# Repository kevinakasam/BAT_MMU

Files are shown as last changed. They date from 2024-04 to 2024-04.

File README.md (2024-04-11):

# The BAT MMU - a simple 2 channel MMU

Side view        |  Top view   |  Hr_Ravn view   
:-------------------------:|:-------------------------:|:-------------------------:
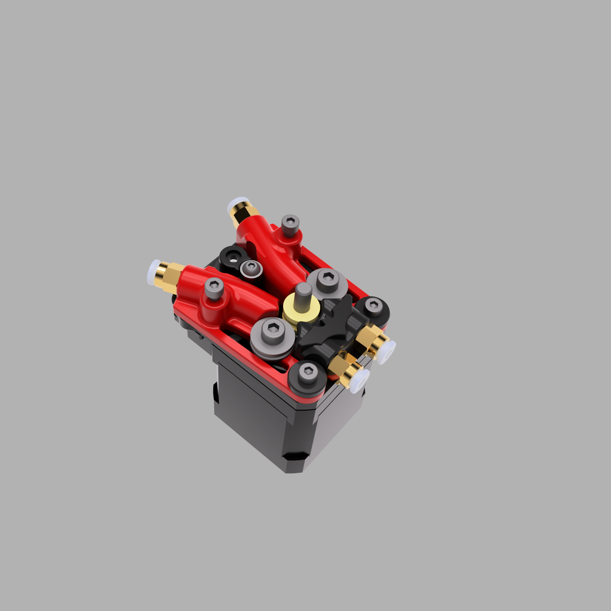
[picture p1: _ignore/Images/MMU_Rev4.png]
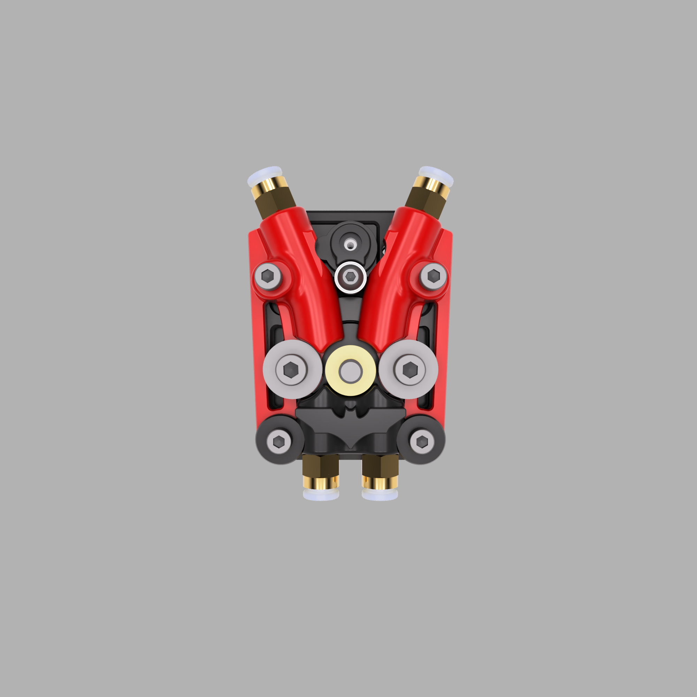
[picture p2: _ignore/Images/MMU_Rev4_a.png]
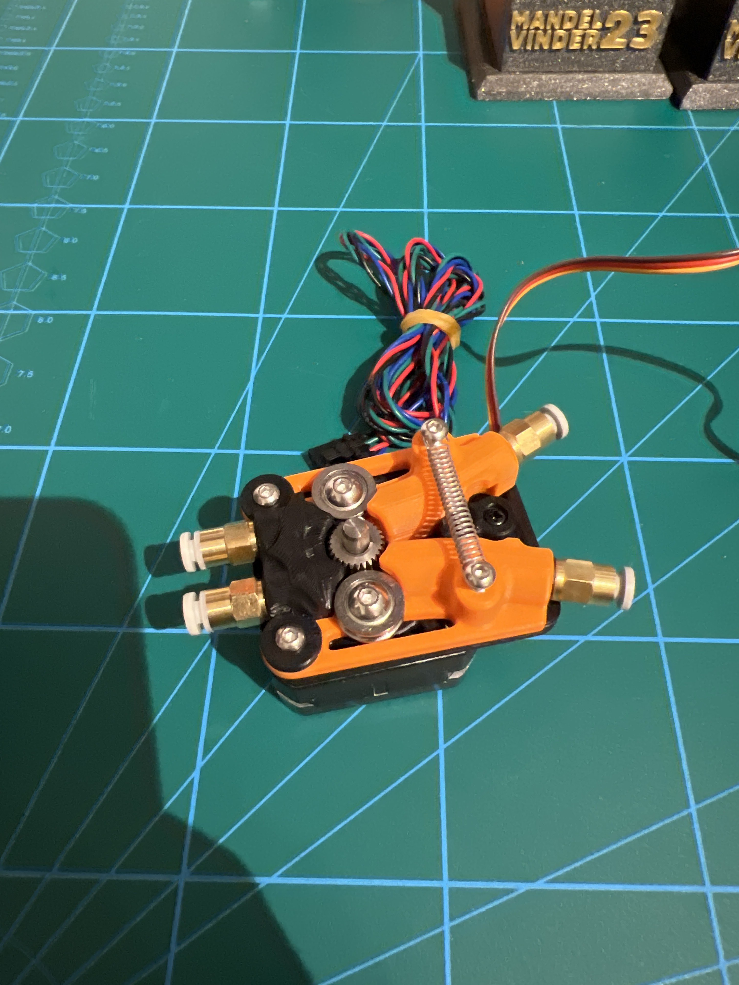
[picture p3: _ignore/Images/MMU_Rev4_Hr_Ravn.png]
  |   |  

Sooo... this is a very old but cool project, I think. I started this project over two years ago, somewhere in 2022, I think. At least, that's when I made the first post about it on Discord. However, let me tell you a bit about the how, why, when, and what's left to do:

### What is this?

It's a two-channel MMU made out of the bare basics you need to swap filaments. That being said, the term MMU, also *Multi* Material Unit, might be a bit over the top as it only swaps two colors (a little spoiler on a crazy idea is at the very end of this page). But two colors are already enough for 95% of the multi-color prints I do, like logos on parts, mesh skirts, and such things. In other words, it's for the lazy people who don't want to swap the colors manually by hand. As another bonus, Bat could also manage two spools on your printer. If you're like me, you print mostly with the same colors, e.g., black and white. So rather than swapping out the filament manually for a (single color) print, you can simply select the filament in the slicer and let the printer check if the correct filament is loaded (that's what I use it for mostly). Or what about a runout manager? In an endless spool mode, Bat *can* / could change the spool once one got empty. There are many use cases for a two-channel MMU, especially for us lazy people.

### How does it work?

Bat is a super simple system which is basically made out of one motor being the extruder and one servo being the selector. Looking at a normal bowden extruder, the motor feeds and retracts one filament by moving back and forward, but for that only *one side* of the extruder is used. Imagine you split a bowden extruder in half and mirror the sides, then you have a filament on each side of it. And this is the basic layout of the Bat MMU. In order to control which filament gets fed / retracted, the servo can move the idler arms on each side of the extruder. By pushing the arm away from the extruder gear, the filament won't move (the filament is deactivated). Due to the spring connection between both arms, the deactivation of one arm (pushing it away) will result in an activation of the other arm. That's it. The only thing we have to account for is that the motor has to spin the other way around for each filament. E.g., a clockwise motor movement feeds Filament A but will retract Filament B. The other way around, we have to invert the motor to feed Filament B / retract Filament A. This might sound a bit confusing, but you can take a look at the little demo video I added to this readme.

#### Demo / Assembly Video

Click on the image to get to the YouTube video:

<a href="https://youtu.be/mqmhv5pWaTc
" target="_blank">MMU Assembly</a> 

### BOM - What do I need to build one?

Coming from the Ender 3 ecosystem, the Bat MMU reuses basically the stock bowden extruder. Varying hardware shouldn't be too much work; I simply used what I have on hand. Modifying the parts e.g. for BMG gears shouldn't be that hard (due to their gears they would also act as dual drive). After building so many [Papilio's](https://kevinakasam.com/papilio/), I have an army of LGX / HGX extruder gears laying around, I thought about to use for a BAT MMU. But that's future talk.

**Here's what you need to build a Bat MMU and its supported alternatives:** [Google Spreadsheet](https://docs.google.com/spreadsheets/d/1bSXrbz5Jo8a5GIIJkao1ZaGwCmv6FLKUNqkR6fM1aHM/edit?usp=sharing) 

##### Alternatives / Experimentals

__Spring__

You can use a printed spring for testing, but I recommend a metal spring to get more tension on the filament. If your reversed bowden setup is very smooth, the printed one will do the job as well, but I don't have a long-time experience with it.

__Bearing__

You can use a printed bearing on the servo arm instead of a proper bearing. Thanks to Thomas for the idea! All the bearing has to do is to reduce the friction between the servo arm and the filament arms. By having a (printed) bearing on the arm, there aren't any rubbing faces, so the servo has an easier job.

### Why is it called Bat MMU?

In the first versions, the Servo was on top of the MMU unit to switch the arms. The shape of the servo reminded me of a bat, and then I made it look like an actual bat, and yeah, that gave it its name. Now, with the newest revision, the servo has moved, and the arm doesn't look like a bat anymore, but I still modeled one on there, so it's still a Bat MMU 😛 and you can also see the two filament arms as wings, so Bat again.

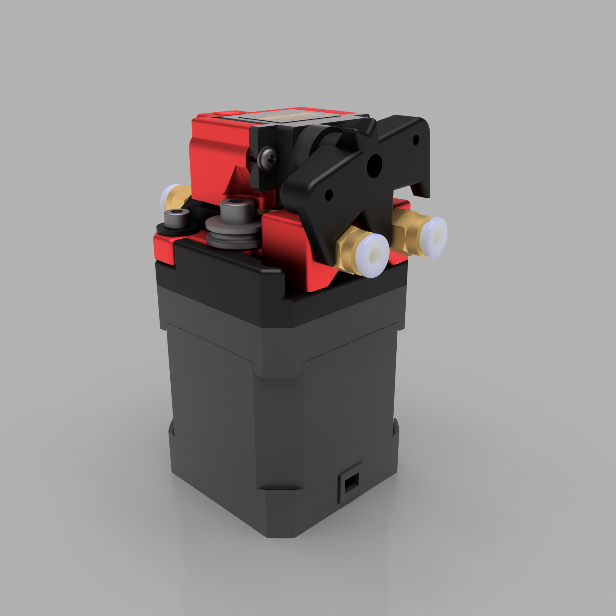
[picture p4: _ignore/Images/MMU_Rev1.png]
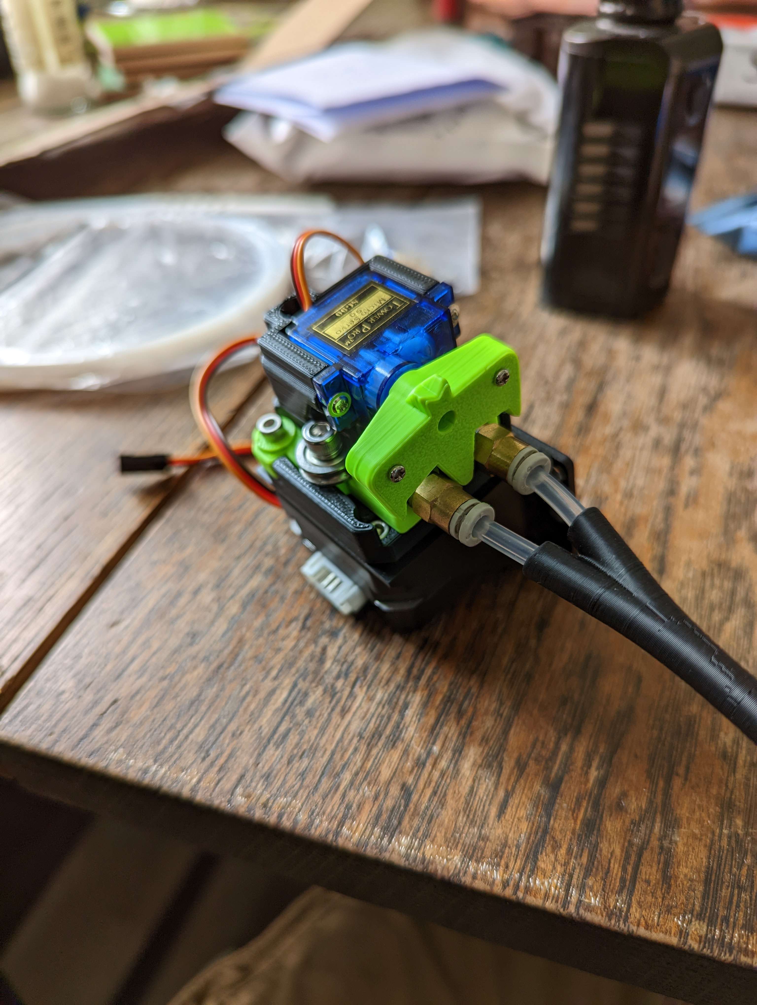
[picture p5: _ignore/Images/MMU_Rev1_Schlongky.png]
   

### The elephant in the room: What's left to do? / What the hell is this hacky code?

Yep, that's right. I might have the skills to sketch something up in CAD, but hell no, I'm not a programmer. I don't want to tell you that I spent easily over 100 hours making these Macros because they're kinda hacky. They do work, that's a plus, but it really relies on saving variables which isn't ideal for the system load, it double-checks some things, sometimes it's smarter than you and does unexpected things, and I think I really overcomplicated it. So far, you can use it for swapping filaments or multi-color prints, and it always remembers which filament is loaded, but functions like the mentioned endless spool mode aren't implemented yet.

##### Bugs

Known bugs are that the pausing during an error doesn't really pause the printer as it tries to complete the load/unload sequence, and for some reason, the movement logic for Filament B gets inverted on its own, no matter what the direction variable is set to (so it still does the right thing, but I don't know where it takes the knowledge from to move that way). Also, the idea to add unique Error codes didn't work out as planned because at some point I only used copy and paste and completely lost track of the numbering.

##### My hacky Macros 

As I have zero knowledge about writing any Python code for this, I had to use Klipper Macros to get this done. This means linking the MMU to the extruder for the final loading wasn't that easy, and I had to trick Klipper for that. By using the `[duplicate_pin_override]`, I could trick Klipper to believe that there are two motors on the MMU, one for feeding the filament to the extruder and one that *extrudes* the filament together with the actual extruder to load it into the nozzle (synced movement between MMU and extruder for loading). That way, the `manual_stepper BATMMU_stepper` and the `extruder_stepper BATMMU_extruder_stepper` are completely identical in the setup for pins, etc., but can be used differently with Klipper. The `manual_stepper BATMMU_stepper` takes care of all the filament movements to the extruder entry; from that point on, the `extruder_stepper BATMMU_extruder_stepper` does all movements together with the actual extruder till the toolhead sensor is triggered.

In short: The Code works, but the Code is evil.

##### My Dream of Happy Hare

It would be a dream to get [Happy Hare](https://github.com/moggieuk/Happy-Hare) support on this, but I don't know how as there's no homing sequence with an endstop involved (my code relies on the saved loaded filament variables), and we don't even have a selector. I think that could be a fun challenge, and if it works, we have a wonderful Bat MMU because the design itself works perfectly fine and so does Happy Hare.

### Are two channels all we can get?

Mh, no. I have two ideas I want to share with you. First, imagine a stack of two Bat MMUs on one stepper, so with two arms per side on top of each other. All they need are two more positions on the servo arm so still only one of the arms is activated / 3 are deactivated. I already started that at some point but never made it to a real design.

Second idea: Add a planetary drive. This will only make sense to you if you're familiar with planetary drives. Planetary drives have the advantage of having three moving components. Setting one as an input, there are always two left that can act as an output. This is partially correct as one of the two has to be stationary to make the planetary work. But setting the Sun as the input (the motor), there are the planets as output if the ring is stationary, or the ring as output if the planets are stationary. You can play around with that in this very cool simulator (https://www.thecatalystis.com/gears/) or watch this simulation: https://www.tec-science.com/wp-content/uploads/2018/09/en-planetary-gear-operation-modi.mp4

So maybe you got my idea already, but with a servo, we should be able to switch the planetary drive between these two output modes. This also means that one output can act as a selector and the other as a feeder. I started with a circular design with the planetary drive in the middle and all the filament paths around it. With that, you can theoretically use an infinite amount of filaments with the MMU; all you have to do is to increase the diameter of the planetary drive. An alternative idea was to use a more linear setup like from the ercf where the planetary gear drives along. All this is still very much in the "I had an idea" state, but I think this is super exciting as you could get infinite channels out of 10€ hardware.

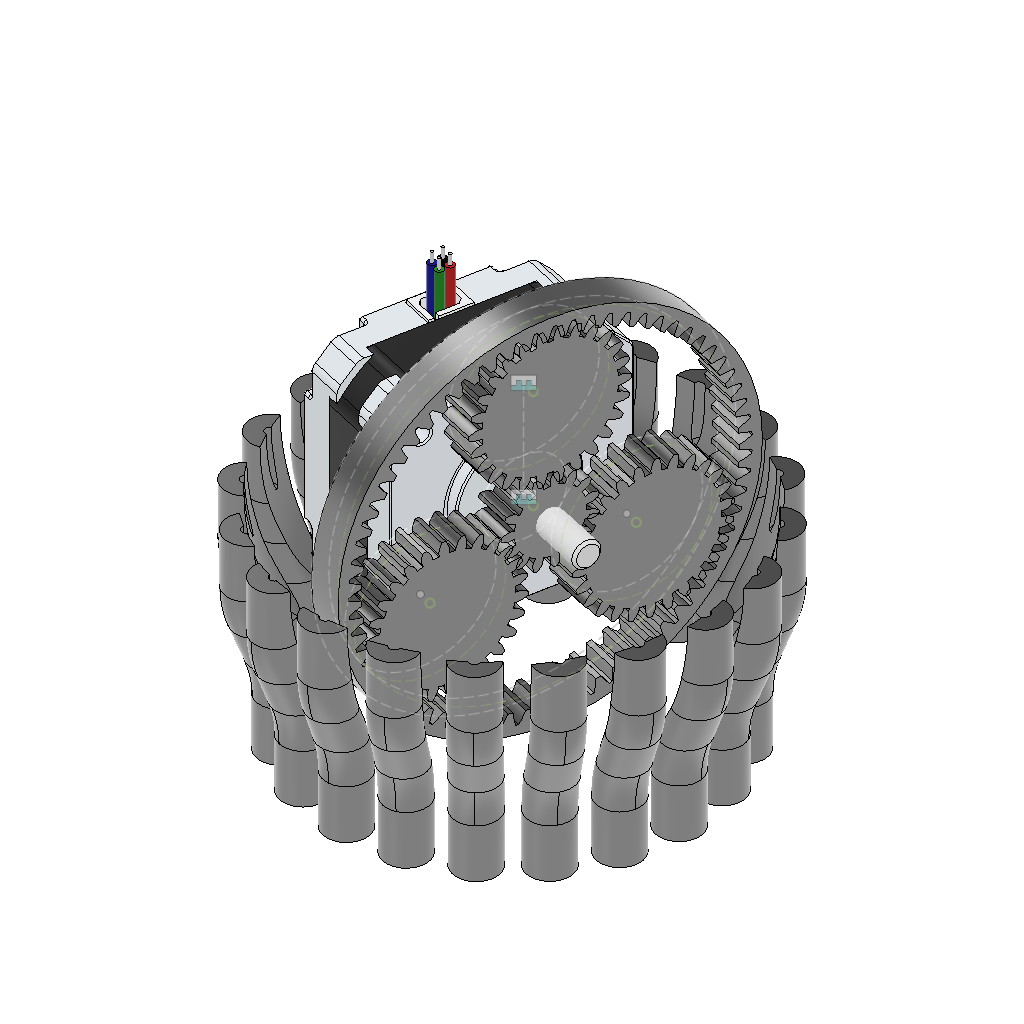
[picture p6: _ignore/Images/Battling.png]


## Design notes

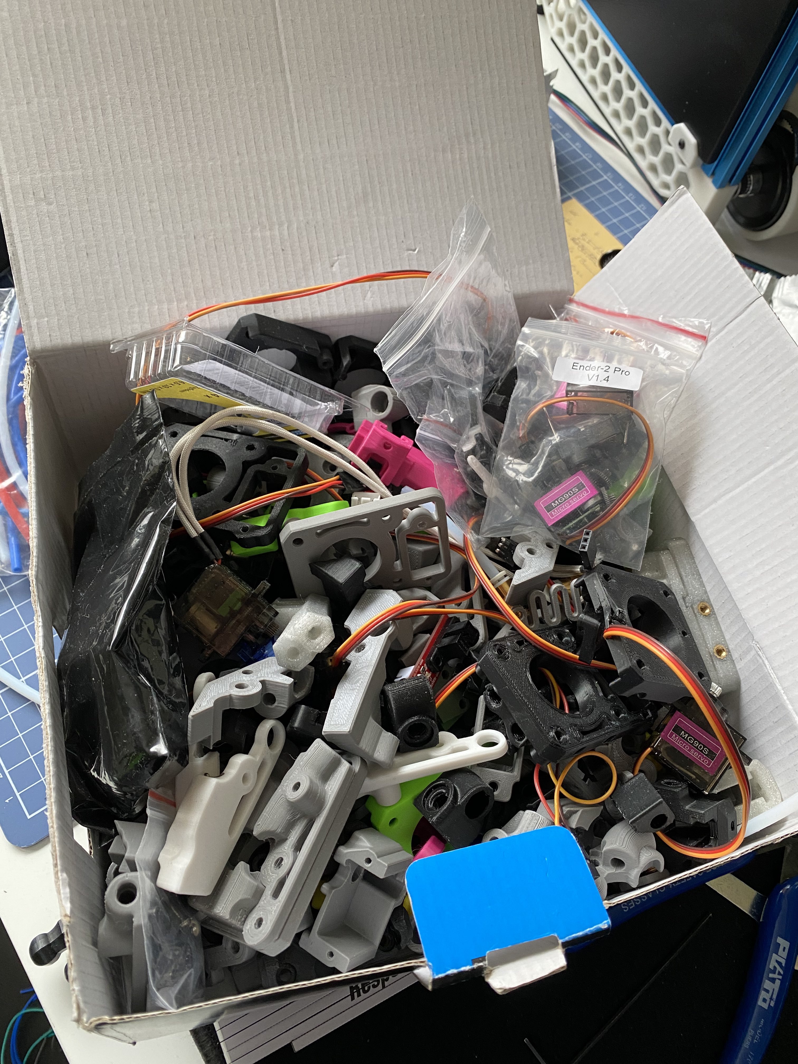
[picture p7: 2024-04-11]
_ignore/Images/its_fun_they_said.png

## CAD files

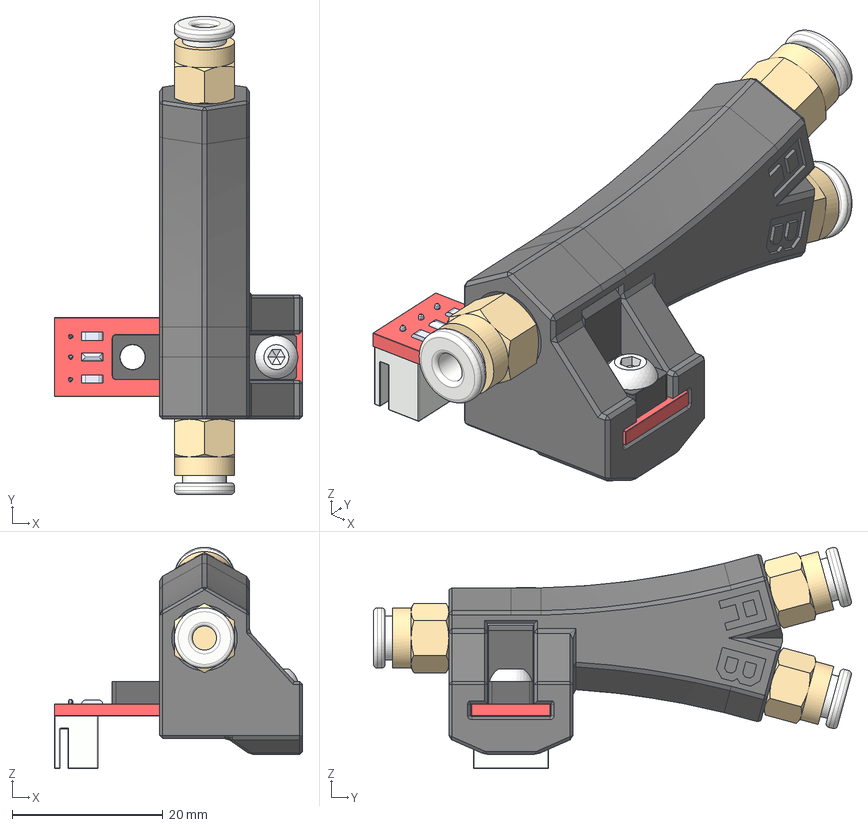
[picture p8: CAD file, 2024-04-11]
CAD/Optical_Y_Splitter_M6.step
33.0 x 63.5 x 29.4 mm
Optical Switch v1
SmartYSplitter
M6 Pneumatic joint x 2
M6 Pneumatic joint v2(Mirror)
M3X8 BHSC v1

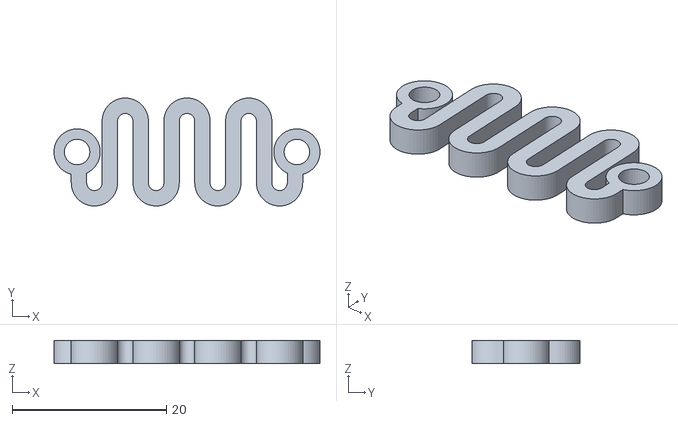
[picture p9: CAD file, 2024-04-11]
STL/MMU/Spring_printed_experimental.stl
34.5 x 14.0 x 3.00

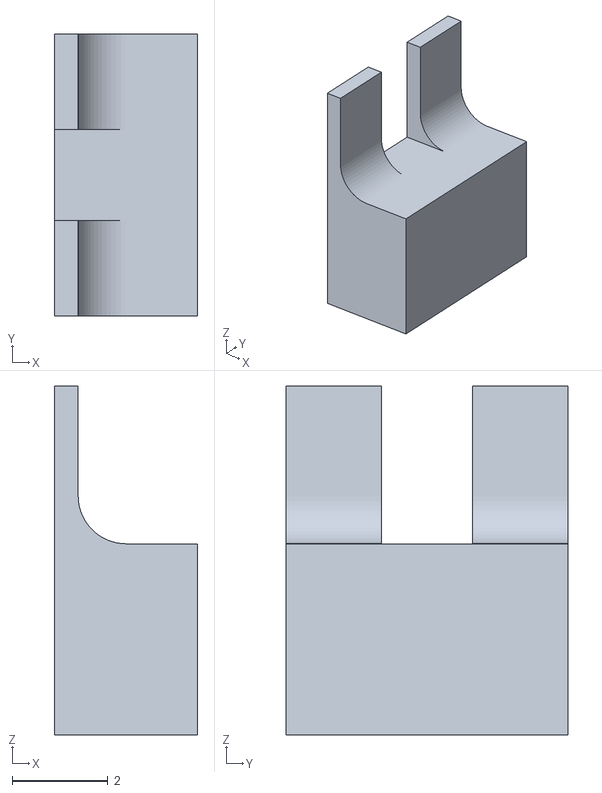
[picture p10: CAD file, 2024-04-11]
STL/Y Splitter/Optical_Y_Guide_Piece_For_Sensor.stl
3.00 x 5.90 x 7.30

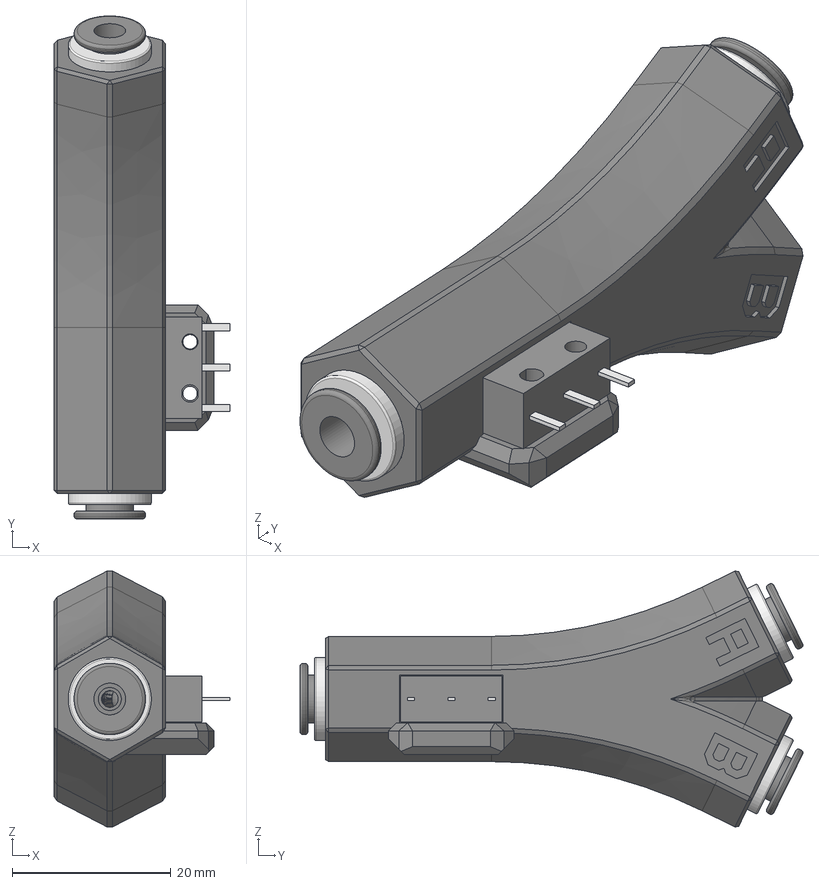
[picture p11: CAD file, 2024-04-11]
CAD/Omron_Y_Splitter_M10_and_ECAS.step
22.1 x 63.3 x 32.2 mm
SmartYSplitter
Omron_D2F_F v1
ECAS04 Bowden Collet v2 x 3

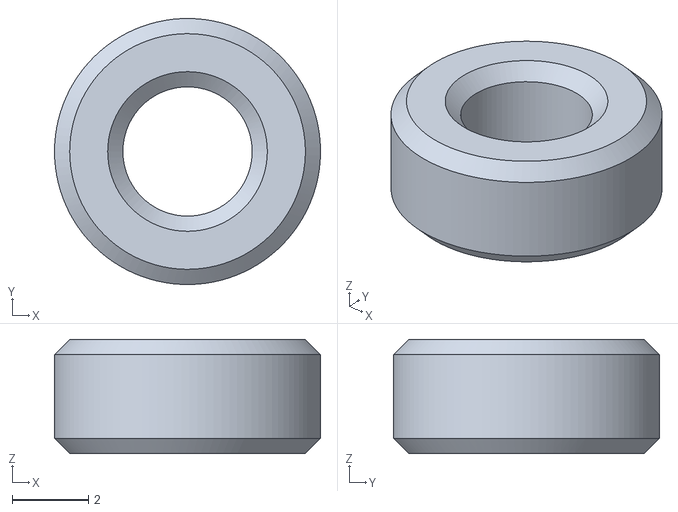
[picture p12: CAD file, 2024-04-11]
STL/MMU/ServoArm_Bearing_Printed_Experimental.stl
7.00 x 7.00 x 3.00

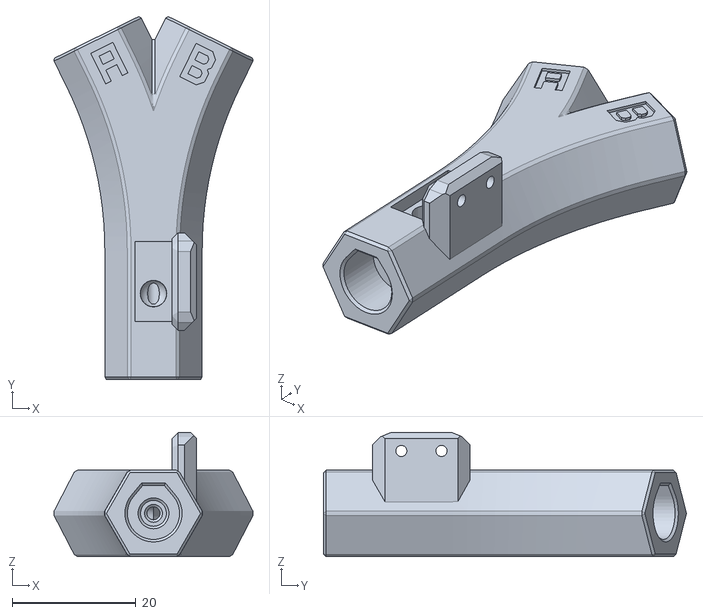
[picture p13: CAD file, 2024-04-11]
STL/Y Splitter/Omron_Y_ECAS.stl
32.2 x 58.8 x 20.1

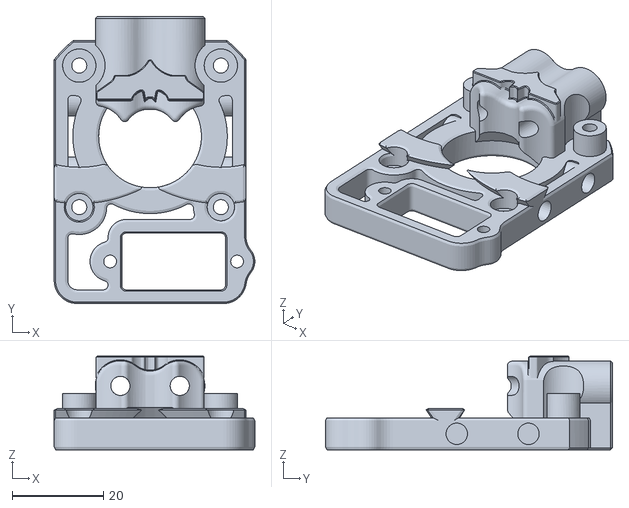
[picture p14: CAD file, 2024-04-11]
STL/MMU/Base_ECAS.stl
43.9 x 62.8 x 20.5

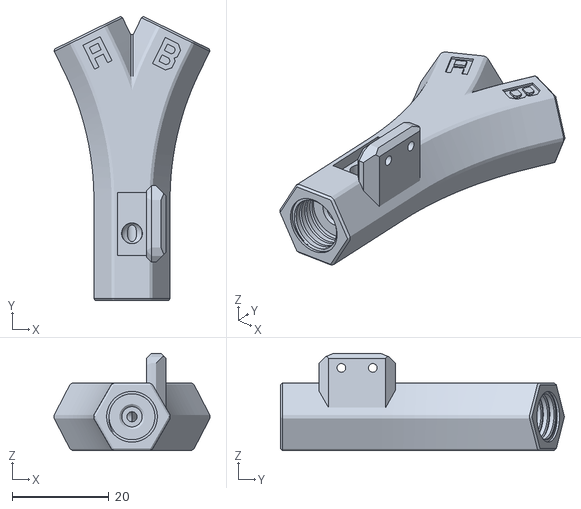
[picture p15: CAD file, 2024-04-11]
STL/Y Splitter/Omron_Y_M10.stl
32.2 x 58.8 x 20.1

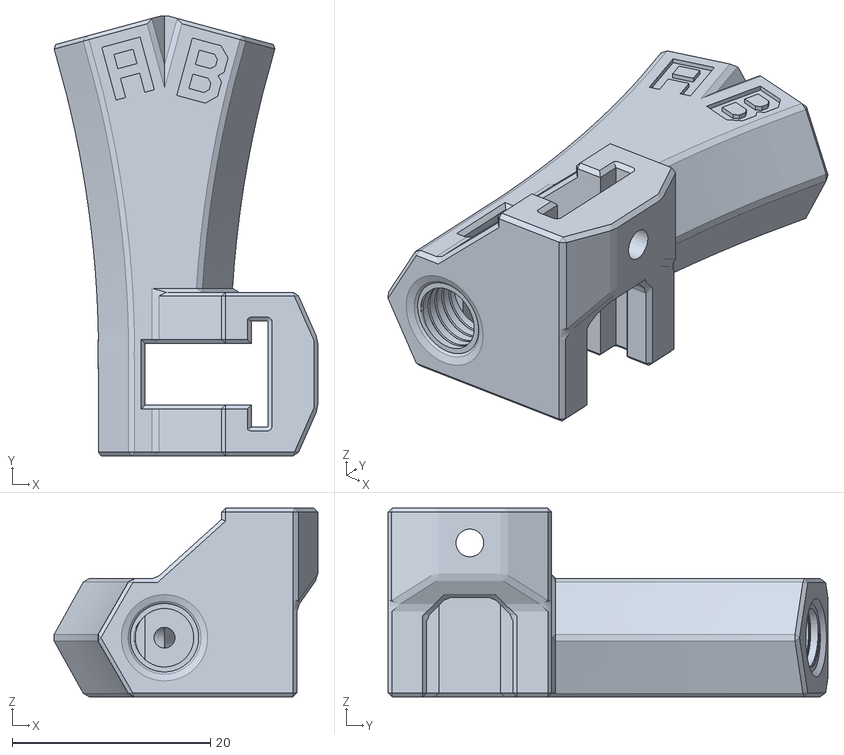
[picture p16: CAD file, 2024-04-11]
STL/Y Splitter/Optical_Y_M6.stl
26.6 x 44.3 x 19.0

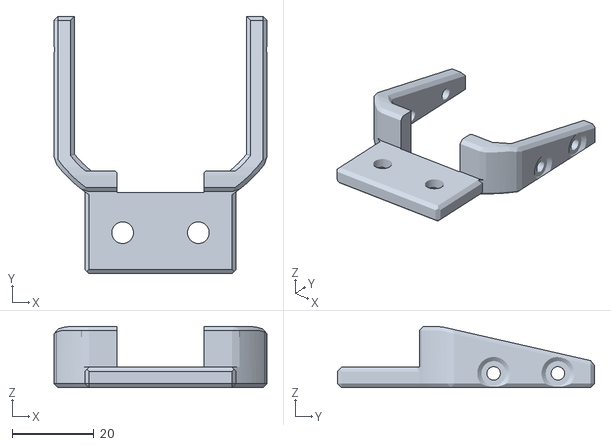
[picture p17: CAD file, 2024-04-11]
STL/MMU/2020_Mount.stl
52.0 x 62.8 x 15.0

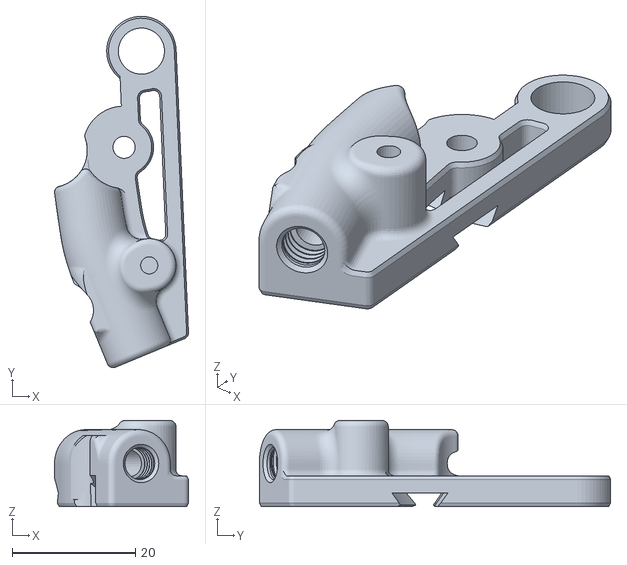
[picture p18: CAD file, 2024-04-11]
STL/MMU/ArmB.stl
21.8 x 57.1 x 14.0

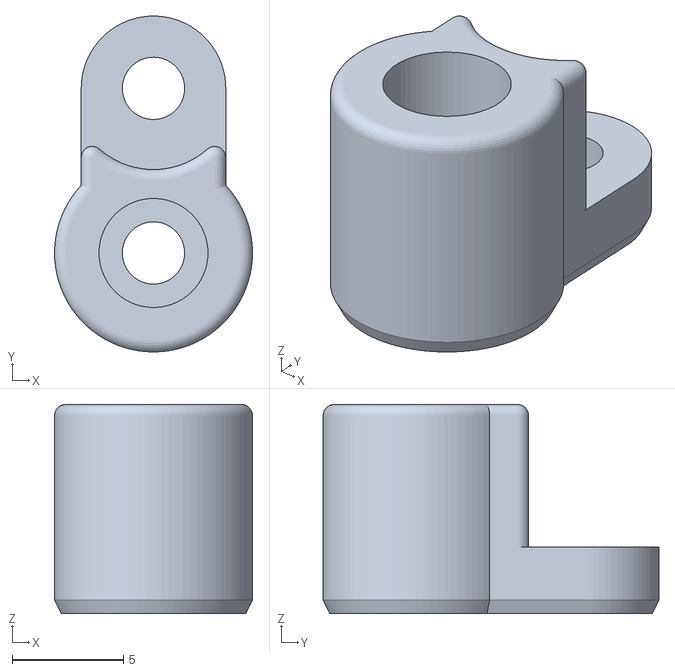
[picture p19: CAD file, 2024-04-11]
STL/MMU/ServoArm.stl
8.90 x 15.1 x 9.40

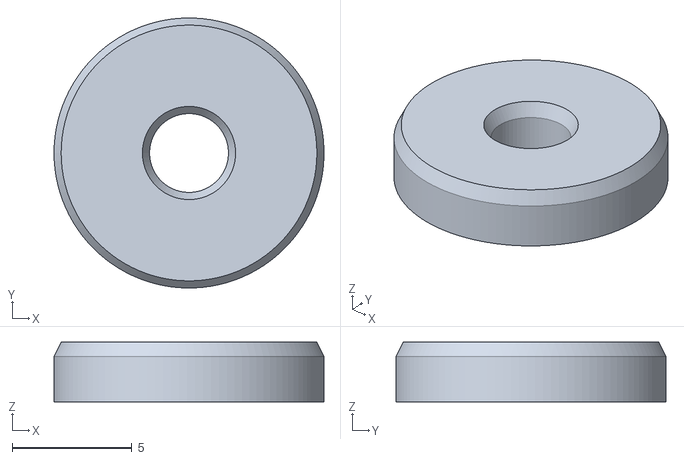
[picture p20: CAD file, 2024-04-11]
STL/MMU/Washer_x2.stl
11.3 x 11.3 x 2.50

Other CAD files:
STL/MMU/ArmA.stl

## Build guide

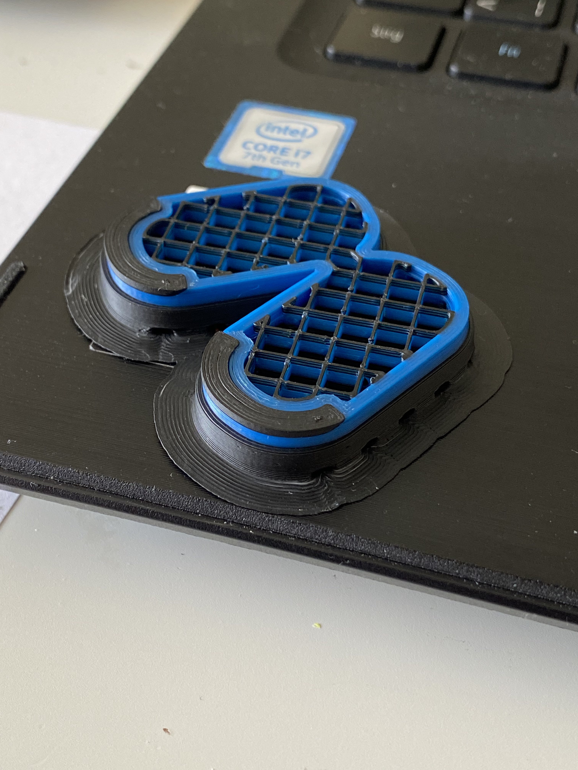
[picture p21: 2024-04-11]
_ignore/Images/print.png

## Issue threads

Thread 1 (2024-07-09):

Happy Hare support

moggieuk, 2024-07-09:
Happy Hare support is quite easy but needs me to finish a few details to make it work -- mainly around tolerating lack of some configuration.  Already no selector is required, etc.  Just need some free time, but this will be done soon.

SpeCter, 2024-07-12:
> Happy Hare support is quite easy but needs me to finish a few details to make it work -- mainly around tolerating lack of some configuration. Already no selector is required, etc. Just need some free time, but this will be done soon.
>
> Other than use of servo for "selector" rather than stepper motor, don't you need the opposite extruder direction for the second tool?

If I understood the current implementation correctly, it does the direction change through the hacky use of [duplicate_pin_override]

kevinakasam, 2024-07-21:
How did I miss this! Sorry!

> Other than use of servo for "selector" rather than stepper motor, don't you need the opposite extruder direction for the second tool?
Yes exactly! The Motor has to spin the other way around for feeding Filament B compared to Filament A. Don't as me why, but in my code that happened somewhat on it's own. I added a variable to invert the extruder direction, but without using it, Klipper does it automatically.

qwuille, 2024-09-28:
If you want a tester, i have everything setup. Haven't gotten the accompanied macros to play along :/

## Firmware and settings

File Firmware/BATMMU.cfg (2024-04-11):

#####################################################################
# To-Do
#####################################################################
# 1. Makro for selecting modes
# 2. Programm a Y-Splitter runout Makro that uses 1. to perform an action
# 3. Clean up Makro logic and remove double checks as well as unneeded variable savings 
# 4. Find a solution that the pause really pauses the printer
# 5. Add a custom unload and load temps per filament, best case with cusom gcode in slicer


#####################################################################
# How-To Setup
#####################################################################
# I recommend to use Orcaslicer for now because it's very easy to setup a MMU setup (simply click on the plus sign on the filament section, that's it) and it doesnt add any gcode for ramming, extruding etc. with the purge tower.

### Orca Slicer ###
# Nothing has to be done in the slicer, it will call the correct macros automatically

### SuSi ###
# Set '_SET_TOOL[next_extruder]' for the 'Tool change G-code' in the 'Printer Settings -> Custom G-code'
# Also you have to set the 'Extruder' number to 2 and check 'Single Extruder Multi Material' in 'Printer Settings -> General -> Capabilities'

# Note that any purge sequence in your start macro isn't needed for dual color printing since we have the purge tower.
# For single color: If you pass the variable of the initial tool with your start gcode you could load the filament before you do the purge line, would look like that:

# Slicer: 'START_PRINT EXTRUDER_TEMP=[nozzle_temperature_initial_layer] BED_TEMP=[bed_temperature_initial_layer] FILAMENT=[initial_tool]'

# Start Gcode:
#[gcode_macro START_PRINT]
#gcode:
    # Add the following two lines to the very top of your start gcode, like here (without the '#' at the beginning).
    # {% set initialfilament = params.initialfilament|default(0)|int %}
    # SAVE_VARIABLE VARIABLE=initialfilament VALUE={initialfilament}
    # ...
    # ... Bed and Nozzle heating, bedmesh etc.
    # ...
    # Add the macro '_INITIATE_MMU' just before you do your purging and it will load the filament it will use first / for the print. 
    # _INITIATE_MMU
    # M117 Purge line
	# PURGE_LINE
    # ...
    # Whatever you do after the purge line
    # ...

#####################################################################
# Include
#####################################################################
[include Macros/common_movements.cfg]
[include Macros/Filament_A.cfg]
[include Macros/Filament_B.cfg]
[include Macros/Pause_Resume.cfg]
[include Macros/Sensor_checks.cfg]
[include Macros/Slicer_macros.cfg]
[include Macros/Tip_forming.cfg]
[include Macros/Tip_forming_Annex.cfg]
[include Macros/Tip_forming_Jon.cfg]
[include Macros/Variable_settings.cfg]

### Optional
[include Macros/extras.cfg]
#####################################################################
# Hardware Section
#####################################################################
[duplicate_pin_override]
pins: EBBCan:PB6, PC6, PB15, PC7, PC10
#   A comma separated list of pins that may be used multiple times in
#   a config file without normal error checks. This parameter must be
#   provided.

#[mcu bat]
#serial: /dev/serial/by-id/usb-FTDI_FT232R_USB_UART_AH06PIM1-if00-port0

[servo BATMMU_servo]
pin: PA1 # Servo Port on SKR Mini E3 DIP
maximum_servo_angle: 180
minimum_pulse_width: 0.00025
maximum_pulse_width: 0.0024

# BAT-MMU Feeder
[manual_stepper BATMMU_stepper]
step_pin: PC6
dir_pin: PB15
enable_pin: !PC7
microsteps: 8
##	rotation_distance = <previous_rotation_distance> * <actual_extrude_distance> / 100
rotation_distance: 32.77872
full_steps_per_rotation: 200	#200 for 1.8 degree, 400 for 0.9 degree
velocity: 200
accel: 1000
endstop_pin: EBBCan:PB6

[tmc2209 manual_stepper BATMMU_stepper]
# Adapt accordingly to your setup and desires
# The default values are tested with the BOM NEMA14 motor
# Please adapt those values to the motor you are using
# Example : for NEMA17 motors, you'll usually set the stealthchop_threshold to 0
# and use higher current
uart_pin: PC10
interpolate: True
run_current: 0.40
#hold_current: 0.1
sense_resistor: 0.110
stealthchop_threshold: 0 

[extruder_stepper BATMMU_extruder_stepper]
extruder:
#   The extruder this stepper is synchronized to. If this is set to an
#   empty string then the stepper will not be synchronized to an
#   extruder. This parameter must be provided.
step_pin: PC6
dir_pin: PB15
enable_pin: !PC7
microsteps: 8
##	rotation_distance = <previous_rotation_distance> * <actual_extrude_distance> / 100
rotation_distance: 32.77872
full_steps_per_rotation: 200	#200 for 1.8 degree, 400 for 0.9 degree


[filament_switch_sensor load_check_sensor]
pause_on_runout: False
#   When set to True, a PAUSE will execute immediately after a runout
#   is detected. Note that if pause_on_runout is False and the
#   runout_gcode is omitted then runout detection is disabled. Default
#   is True.
#runout_gcode: 
#   A list of G-Code commands to execute after a filament runout is
#   detected. See docs/Command_Templates.md for G-Code format. If
#   pause_on_runout is set to True this G-Code will run after the
#   PAUSE is complete. The default is not to run any G-Code commands.
#insert_gcode:
#   A list of G-Code commands to execute after a filament insert is
#   detected. See docs/Command_Templates.md for G-Code format. The
#   default is not to run any G-Code commands, which disables insert
#   detection.
event_delay: 0.1
#   The minimum amount of time in seconds to delay between events.
#   Events triggered during this time period will be silently
#   ignored. The default is 3 seconds.
#pause_delay: 0.5
#   The amount of time to delay, in seconds, between the pause command
#   dispatch and execution of the runout_gcode. It may be useful to
#   increase this delay if OctoPrint exhibits strange pause behavior.
#   Default is 0.5 seconds.
switch_pin: ^EBBCan:PB6
#   The pin on which the switch is connected. This parameter must be
#   provided.

[filament_switch_sensor toolhead_sensor]
pause_on_runout: False
#   When set to True, a PAUSE will execute immediately after a runout
#   is detected. Note that if pause_on_runout is False and the
#   runout_gcode is omitted then runout detection is disabled. Default
#   is True.
#runout_gcode: 
#   A list of G-Code commands to execute after a filament runout is
#   detected. See docs/Command_Templates.md for G-Code format. If
#   pause_on_runout is set to True this G-Code will run after the
#   PAUSE is complete. The default is not to run any G-Code commands.
#insert_gcode: _DEACTIVATE_BATMMU_EXTRUDER_STEPPER
#   A list of G-Code commands to execute after a filament insert is
#   detected. See docs/Command_Templates.md for G-Code format. The
#   default is not to run any G-Code commands, which disables insert
#   detection.
event_delay: 0.1
#   The minimum amount of time in seconds to delay between events.
#   Events triggered during this time period will be silently
#   ignored. The default is 3 seconds.
#pause_delay: 0.5
#   The amount of time to delay, in seconds, between the pause command
#   dispatch and execution of the runout_gcode. It may be useful to
#   increase this delay if OctoPrint exhibits strange pause behavior.
#   Default is 0.5 seconds.
switch_pin: ^EBBCan:PB3
#   The pin on which the switch is connected. This parameter must be
#   provided.


#####################################################################
# Setup -- Variables
#####################################################################
[gcode_macro _BATMMU_VAR]
description: Empty macro to store the variables
### Servo ###
variable_servo_filament_a_angle: 120
variable_servo_neurtal_angle: 110
variable_servo_filament_b_angle: 180

### Bowden-Lengths I ###
variable_bowdenlength_a_mmu_to_y: 370      #Roughly measure the length of your bowden tube between MMU and Y-Splitter
variable_bowdenlength_b_mmu_to_y: 370      #Roughly measure the length of your bowden tube between MMU and Y-Splitter
variable_bowdenlength_y_to_extruder: 185   #Roughly measure the length of your bowden tube between Y-Splitter and Extruder
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

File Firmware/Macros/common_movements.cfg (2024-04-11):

#################################################################
#### Klipper - Makros // Macros you can see on the Dashboard ####
#################################################################

###########
## Servo ##
###########
[gcode_macro NEUTRAL]
description: Set Servo in neutral position
gcode:
    {% set batvar = printer["gcode_macro _BATMMU_VAR"] %}
    SET_SERVO SERVO=BATMMU_servo ANGLE={batvar.servo_neurtal_angle}
    SET_SERVO SERVO=BATMMU_servo WIDTH=0.0
    G4 P{batvar.servo_idle_time}

###################
## Test - Makros ##
###################
[gcode_macro mmu_move_100]
description: Test Stepper, check esteps
gcode:
    MANUAL_STEPPER STEPPER=BATMMU_stepper SET_POSITION=0
    MANUAL_STEPPER STEPPER=BATMMU_stepper MOVE={100} SPEED=50 ACCEL=100 SYNC=0
    G4 P0 #Don't remove this or the macro will stop working

##################################################################
#### Helper - Makros // Macros you can't see on the Dashboard ####
##################################################################

################
## Brain Mako ##
################

[gcode_macro _SET_TOOLS]
description: Prepare printer to print with Filament B.
gcode:
    _IS_Y_FREE_TO_LOAD_FILAMENT
    _IS_Y_FREE_TO_LOAD_FILAMENT #Macro has to be called two times so the variables get set properly
    _IS_EXTRUDER_FREE_TO_LOAD_FILAMENT
    _IS_EXTRUDER_FREE_TO_LOAD_FILAMENT #Macro has to be called two times so the variables get set properly
    _SET_TOOLS_MOVE

[gcode_macro _SET_TOOLS_MOVE]
description: Prepare printer to print with Filament B.
gcode:
    {% set batvar = printer["gcode_macro _BATMMU_VAR"] %}
    {% set batsavedvar = printer.save_variables.variables %}

## Filament is already loaded
    {% if printer["gcode_macro _IS_Y_FREE_TO_LOAD_FILAMENT"].is_y_free_to_load_filament == 11 %}
        M118 Filament A is already loaded.
    {% endif %}
    {% if printer["gcode_macro _IS_Y_FREE_TO_LOAD_FILAMENT"].is_y_free_to_load_filament == 22 %}
        M118 Filament B is already loaded.
    {% endif %}

## Free to load
    {% if printer["gcode_macro _IS_Y_FREE_TO_LOAD_FILAMENT"].is_y_free_to_load_filament == True %}
        {% if printer["gcode_macro _IS_EXTRUDER_FREE_TO_LOAD_FILAMENT"].is_extruder_free_to_load_filament == True %}
          M118 Y is free...
          _LOAD_FILAMENT
        {% endif %}
    {% endif %}

## Free to load but variables aren't correct
    {% if printer["gcode_macro _IS_Y_FREE_TO_LOAD_FILAMENT"].is_y_free_to_load_filament == 10 %}
        M118 BatErr002a: Filament A is set as loaded but sensors are not triggered.
        M118 Reset loaded filament to none and continue preparing... Tststs, did you unload the filament by hand?
        _SET_LOADED_FILAMENT_NONE
        _LOAD_FILAMENT
    {% endif %}
    {% if printer["gcode_macro _IS_Y_FREE_TO_LOAD_FILAMENT"].is_y_free_to_load_filament == 20 %}
        M118 BatErr002b: Filament B is set as loaded but sensors are not triggered.
        M118 Reset loaded filament to none and continue preparing... Tststs, did you unload the filament by hand?
        _SET_LOADED_FILAMENT_NONE
        _LOAD_FILAMENT
    {% endif %}

## Unload other Filament first
    {% if printer["gcode_macro _IS_Y_FREE_TO_LOAD_FILAMENT"].is_y_free_to_load_filament == 12 %}
        M118 Filament B is loaded, unloading it and load Filament A.
        _UNLOAD_FILAMENT_B
        _LOAD_FILAMENT_A
    {% endif %}
    {% if printer["gcode_macro _IS_Y_FREE_TO_LOAD_FILAMENT"].is_y_free_to_load_filament == 21 %}
        M118 Filament A is loaded, unloading it and load Filament B.
        _UNLOAD_FILAMENT_A
        _LOAD_FILAMENT_B
    {% endif %}

### Error
    {% if printer["gcode_macro _IS_Y_FREE_TO_LOAD_FILAMENT"].is_y_free_to_load_filament == 00 %}
        M118 BatErr333: an unknown filament is loaded!
        M118 Use _SET_LOADED_FILAMENT_A or _SET_LOADED_FILAMENT_B to set the correct Filament that is loaded. Then use _RESUME_MMU and then rerun the command.
        _PAUSE_MMU
    {% endif %}

    {% if printer["gcode_macro _IS_Y_FREE_TO_LOAD_FILAMENT"].is_y_free_to_load_filament == False %}
        M118 BatErr333: Filament is stuck in Y-Splitter!
        _PAUSE_MMU
    {% endif %}

    {% if printer["gcode_macro _IS_Y_FREE_TO_LOAD_FILAMENT"].is_y_free_to_load_filament == 66 %}
        M118 BatErr333: Big Problem! Filament is stuck in Toolhead!
        _PAUSE_MMU
    {% endif %}

##############
## Loadings ##
##############

## Loading Start

[gcode_macro _LOAD_FILAMENT]
description: Load Filament - movements after checks
gcode:
    {% set retries = 3|int %}
    {% set batsavedvar = printer.save_variables.variables %}
    {% set batvar = printer["gcode_macro _BATMMU_VAR"] %}

        {% if batsavedvar.requested_filament == 1 %}
            {% if printer["gcode_macro _PARK_FILAMENT"].a_is_prepared == False %}
                _PREPARE_FILAMENT
            {% endif %}
            {% if printer["gcode_macro _PARK_FILAMENT"].a_is_prepared == True %}
                FILAMENT_A
            {% endif %}
        {% endif %}
        {% if batsavedvar.requested_filament == 2 %}
            {% if printer["gcode_macro _PARK_FILAMENT"].b_is_prepared == False %}
                _PREPARE_FILAMENT
            {% endif %}
            {% if printer["gcode_macro _PARK_FILAMENT"].b_is_prepared == True %}
                FILAMENT_B
            {% endif %}
        {% endif %}
        _Y_TO_EXTRUDER
        _EXTRUDER_TO_TOOLHEAD_SENSOR
        {% for try in range(retries|int) %}
            _RETRY_EXTRUDER_TO_TOOLHEAD_SENSOR
            M400
        {% endfor %}
        _LOAD_FILAMENT_FINISH

## Loading End
[gcode_macro _LOAD_FILAMENT_FINISH]
description: Load Filament - movements after checks
gcode:
    _IS_FILAMENT_IN_TOOLHEAD
    _LOAD_FILAMENT_FINISH_MOVE

[gcode_macro _LOAD_FILAMENT_FINISH_MOVE]
description: Load Filament - movements after checks
gcode:
    {% if printer["gcode_macro _IS_FILAMENT_IN_TOOLHEAD"].is_filament_in_toolhead == True %}
        _RESET_BATMMU_EXTRUDER_STEPPER
        _TOOLHEAD_SENSOR_TO_NOZZLE
    {% endif %}

################
## Unloadings ##
################

## Unloading start
[gcode_macro _UNLOAD_FILAMENT]
description: Unoad Filament from the Toolhead to the Y-Splitter park-position
gcode:
    _UNLOADING_FILAMENT_CHECK
    _UNLOAD_FILAMENT_MOVE

[gcode_macro _UNLOAD_FILAMENT_MOVE]
description: Unoad Filament from the Toolhead to the Y-Splitter park-position
gcode:
    {% set retries = 3|int %}

    {% if printer["gcode_macro _UNLOADING_FILAMENT_CHECK"].unloading_filament_check == True %}
        _UNLOAD_TOOLHEAD
        {% for try in range(retries|int) %}
            _RETRY_UNLOAD_TOOLHEAD
            M400
        {% endfor %}
    _UNLOAD_FILAMENT_FINISH
    {% endif %}

## Unloading middle
[gcode_macro _UNLOAD_FILAMENT_FINISH]
description: Unoad Filament from the Toolhead to the Y-Splitter park-position
gcode:
    _IS_FILAMENT_OUT_OF_TOOLHEAD
    _UNLOAD_FILAMENT_FINISH_MOVE

[gcode_macro _UNLOAD_FILAMENT_FINISH_MOVE]
description: Unoad Filament from the Toolhead to the Y-Splitter park-position
gcode:
    {% set retries = 3|int %}

    {% if printer["gcode_macro _IS_FILAMENT_OUT_OF_TOOLHEAD"].is_filament_out_of_toolhead == True %}
        _EXTRUDER_TO_Y
         {% for try in range(retries|int) %}
            _RETRY_EXTRUDER_TO_Y
            M400
        {% endfor %}
        _UNLOAD_FILAMENT_FINISH_FINAL
    {% endif %}

## Unloading end
[gcode_macro _UNLOAD_FILAMENT_FINISH_FINAL]
description: Unoad Filament from the Toolhead to the Y-Splitter park-position
gcode:
    _IS_FILAMENT_OUT_Y
    _UNLOAD_FILAMENT_FINISH_FINAL_MOVE

[gcode_macro _UNLOAD_FILAMENT_FINISH_FINAL_MOVE]
description: Unoad Filament from the Toolhead to the Y-Splitter park-position
gcode:
    {% set batvar = printer["gcode_macro _BATMMU_VAR"] %}
    {% set batsavedvar = printer.save_variables.variables %}

    {% if printer["gcode_macro _IS_FILAMENT_OUT_Y"].is_filament_out_y == True %}
        {% if batsavedvar.requested_filament == 1 %}
          _PARK_FILAMENT
          M118 Filament A got unloaded into Y-Splitter.
        {% endif %}
        {% if batsavedvar.requested_filament == 2 %}
          _PARK_FILAMENT
          M118 Filament B got unloaded into Y-Splitter.
        {% endif %}
    {% endif %}

#####################
## Loading helpers ##
#####################

### Before Y-Splitter ###

## Preparing
# Preparing Start
[gcode_macro _PREPARE_FILAMENT]
description: Load Filament to the Y Splitter splitting point
gcode:
    _IS_Y_FREE_TO_LOAD_FILAMENT
    _PREPARE_FILAMENT_MOVE
   

[gcode_macro _PREPARE_FILAMENT_MOVE]
description: Load Filament to the Y Splitter splitting point
gcode:
    {% if printer["gcode_macro _IS_Y_FREE_TO_LOAD_FILAMENT"].is_y_free_to_load_filament == True %}
        {% set retries = 3|int %}
        _MMU_TO_Y
        {% for try in range(retries|int) %}
            _RETRY_MMU_TO_Y
            M400
        {% endfor %}
        _PREPARE_FILAMENT_FINISH
    {% endif %}
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
